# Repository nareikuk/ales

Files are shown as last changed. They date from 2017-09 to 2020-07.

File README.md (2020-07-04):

# ales
Altitude Limiting Electronic Switch for model electric glider competitions

This is still under early development even though it has been under construction since 2016. The aim is to produce a cheap,
easy to construct and simple to use altitude limiting switch for electric motor launched model gliders for competition use.
The schematics, PCB and firmware are all provided. I may be able to supply blank PCBs or even fully populated PCBs in the future,
once the bugs have been ironed out and I'm happy that the project has reached a production quality level.

Note that currently the firmware is working but some improvements required around startup reliability.

The current features of the ALES v2 include:
1) Pre-set altitude cut-off of 100m, 150m or 200m which are the three standards used in competition.
2) Motor run time limited to 30 seconds if pre-set altitude has not been reached before then
3) Auto-calibrates to receiver pulse timing at start up
4) Auto-calibrates altitude of launch field
5) After cut-off, if throttle stick is retuned to idle, the ALES will re-enable motor power after three seconds for those landing emergencies
6) Altitude sampling at 1kHz with better than 0.2m resolution
7) Very small and light hardware profile
8) Works with HV or standard servos and is powered from the receiver, drawing around 2mA
9) 32-bit STM32F0 microcontroller and BMP280 pressure sensor provide the core functionality
10) Single-sided load for all surface mount components

Future features once v2 has reached production quality will include anti-zoom control and field based configuration.

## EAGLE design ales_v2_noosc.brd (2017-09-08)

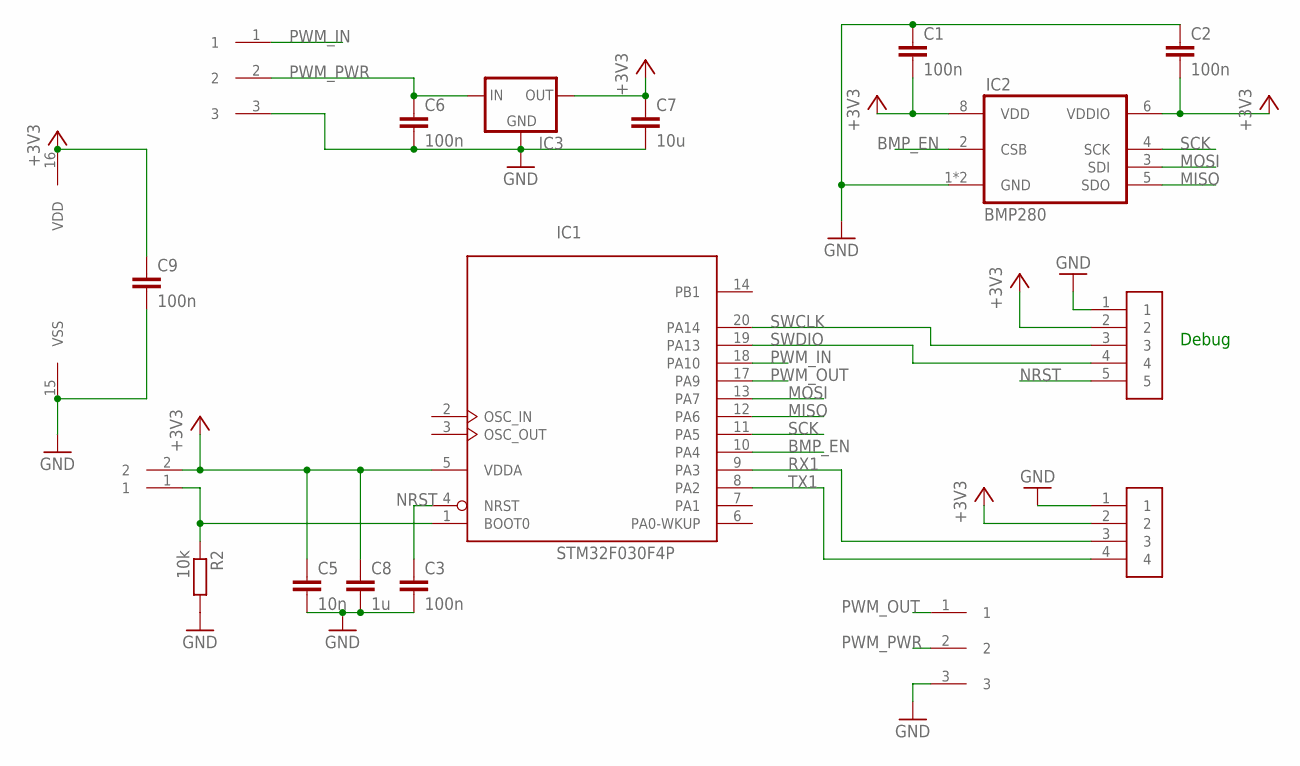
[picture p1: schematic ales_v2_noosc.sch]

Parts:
BOOT: SMD_CONN1X2; CONN_SMD1X2
C1, C2, C3, C6, C9: 100n; C0603K
C5: 10n; C0603K
C7: 10u; C0603K
C8: 1u; C0603K
IC1: STM32F030F4P; TSSOP20-I
IC2: BMP280
IC3: XC63FPM; SOT23
R2: 10k; R0603
U$2, U$3: CONN1X3
U$4: CONN1X4
U$6: CONN1X5

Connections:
+3V3: BOOT.2, C1.2, C2.2, C5.1, C7.1, C8.1, C9.1, IC1.5 (VDDA), IC1.16 (VDD), IC2.6 (VDDIO), IC2.8 (VDD), IC3.1 (OUT), U$4.2, U$6.2
BMP_EN: IC1.10 (PA4), IC2.2 (CSB)
BOOT0: BOOT.1, IC1.1 (BOOT0), R2.1
GND: C1.1, C2.1, C3.2, C5.2, C6.2, C7.2, C8.2, C9.2, IC1.15 (VSS), IC2.1 (GND), IC2.7 (GND), IC3.3 (GND), R2.2, U$2.3, U$3.3, U$4.1, U$6.1
MISO: IC1.12 (PA6), IC2.5 (SDO)
MOSI: IC1.13 (PA7), IC2.3 (SDI)
NRST: C3.1, IC1.4 (NRST), U$6.5
PWM_IN: IC1.18 (PA10), U$3.1
PWM_OUT: IC1.17 (PA9), U$2.1
PWM_PWR: C6.1, IC3.2 (IN), U$2.2, U$3.2
RX1: IC1.9 (PA3), U$4.3
SCK: IC1.11 (PA5), IC2.4 (SCK)
SWCLK: IC1.20 (PA14), U$6.3
SWDIO: IC1.19 (PA13), U$6.4
TX1: IC1.8 (PA2), U$4.4

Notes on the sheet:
Debug

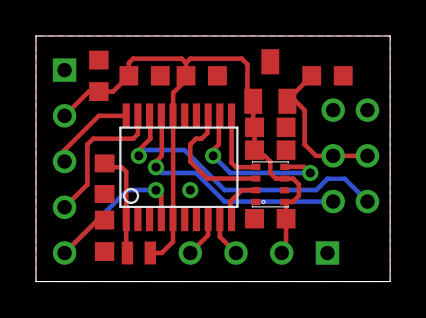
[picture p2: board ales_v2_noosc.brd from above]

Board: 2 copper layers, 19.7 x 13.6 mm, 17 parts (0 on the bottom side), 15 nets.

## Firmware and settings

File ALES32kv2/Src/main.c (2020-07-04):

/**
 ******************************************************************************
 * File Name          : main.c
 * Description        : Main program body
 ******************************************************************************
 *
 * COPYRIGHT(c) 2016 STMicroelectronics
 *
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
 ******************************************************************************
 */
/* Includes ------------------------------------------------------------------*/
#include "stm32f0xx_hal.h"

/* USER CODE BEGIN Includes */
#include "string.h"
/* USER CODE END Includes */

SPI_HandleTypeDef hspi1;

TIM_HandleTypeDef htim1;

UART_HandleTypeDef huart1;

/* USER CODE BEGIN PV */
//SPI_HandleTypeDef SpiHandle;
typedef struct _bmp280calibration {
    uint16_t dig_t1;
    int16_t dig_t2;
    int16_t dig_t3;
    uint16_t dig_p1;
    int16_t dig_p2;
    int16_t dig_p3;
    int16_t dig_p4;
    int16_t dig_p5;
    int16_t dig_p6;
    int16_t dig_p7;
    int16_t dig_p8;
    int16_t dig_p9;
} Bmp280Calibration;

Bmp280Calibration bmpCalibration;

//#define BUFFERSIZE 64

// Pressure differences * 25600 between start alt and height above start alt
#define ALT_100M -1196     // -305995.1386
#define ALT_150M -1789     // -457892.7898
#define ALT_200M -2380     // -609060.7514

#define ALT_CUTOFF ALT_150M    // Change this to set the altimeter cutoff height
#define VERSION "1.4f"

#define RCSAMPLES 8

//#define VERBOSE 1

enum {
    BMP280_REGISTER_DIG_T1 = 0x88,
    BMP280_REGISTER_DIG_T2 = 0x8A,
    BMP280_REGISTER_DIG_T3 = 0x8C,

    BMP280_REGISTER_DIG_P1 = 0x8E,
    BMP280_REGISTER_DIG_P2 = 0x90,
    BMP280_REGISTER_DIG_P3 = 0x92,
    BMP280_REGISTER_DIG_P4 = 0x94,
    BMP280_REGISTER_DIG_P5 = 0x96,
    BMP280_REGISTER_DIG_P6 = 0x98,
    BMP280_REGISTER_DIG_P7 = 0x9A,
    BMP280_REGISTER_DIG_P8 = 0x9C,
    BMP280_REGISTER_DIG_P9 = 0x9E,

    BMP280_REGISTER_CHIPID = 0xD0,
    BMP280_REGISTER_VERSION = 0xD1,
    BMP280_REGISTER_SOFTRESET = 0xE0,

    BMP280_REGISTER_CAL26 = 0xE1,  // R calibration stored in 0xE1-0xF0

    BMP280_REGISTER_CONTROL = 0xF4,
    BMP280_REGISTER_CONFIG = 0xF5,
    BMP280_REGISTER_PRESSUREDATA = 0xF7,
    BMP280_REGISTER_TEMPDATA = 0xFA,
};

typedef int32_t BMP280_S32_t;
typedef uint32_t BMP280_U32_t;
typedef int64_t BMP280_S64_t;

BMP280_S32_t t_fine;
volatile int rxPwm = 0;
int lastCounter = 0;
int counter = 0;

uint8_t throttleActive = 0; // The throttle is allowed to be moved from idle if throttleActive is 1
#ifdef VERBOSE
char strbuf[100];
#endif
/* USER CODE END PV */

void SystemClock_Config(void);
void errorHandler(void);
static void MX_GPIO_Init(void);
static void MX_SPI1_Init(void);
static void MX_TIM1_Init(void);
static void MX_USART1_UART_Init(void);

void HAL_TIM_MspPostInit(TIM_HandleTypeDef *htim);

/* USER CODE BEGIN PFP */
uint8_t bmp280GetChipId(void);
uint8_t bmp280GetCalibration(void);
int32_t spiGetInt20(uint8_t address);
void bmp280Init(void);
BMP280_S32_t bmp280CompensateTemperature(BMP280_S32_t adcTemp);
BMP280_S64_t bmp280PressureDiff(BMP280_S32_t adcPres, BMP280_S64_t startPa);
void timeoutErrorHandler(void);
void itoa(int n, char s[]);

/* USER CODE END PFP */

/* USER CODE BEGIN 0 */
int tFilter[RCSAMPLES] = { 0 };
uint8_t filterCount = 0;

void HAL_TIM_IC_CaptureCallback(TIM_HandleTypeDef *htim) {
    int diff = 0;

    if (htim->Instance == TIM1) {
        // Ideally we'd like to know if the interrupt was due to the rising or falling edge
        // so we can capture the pulse time on the falling edge and start the counter on
        // the rising edge. Until that is figured out, go for a simpler version where we capture
        // two edges and see if the time is short enough to have been a pulse rather than the
        // gap between pulses. A pulse will be shorter than 2500uS (probably only around 2100uS
        // at most). The gap between pulses will be at least 17500uS.
        counter = HAL_TIM_ReadCapturedValue(htim, TIM_CHANNEL_3);
        if (lastCounter > counter) {
            diff = 20000 - lastCounter + counter;
        } else {
            diff = counter - lastCounter;
        }
        lastCounter = counter;

        if (diff < 2500 && diff > 900) { // We must have the pulse time rather than the gap between pulses
            tFilter[filterCount++] = diff;
            filterCount %= RCSAMPLES;

            int avg = 0;
            for (int i = 0; i < RCSAMPLES; i++) {
                avg += tFilter[i];
            }

            rxPwm = avg / RCSAMPLES;
        }

        // TODO: if no pulses received for some time, then set rxPwm to 0 rather than leaving
        //       it stuck at last measured value
    }
}

int waitForIdleThrottle() {
    // Capture idle throttle. Must be below 1200uS and above 900uS for 2 seconds
    uint8_t idleCaptured = 0;
    int idleThrottlePeriod;

    while (!idleCaptured) {
        int throttle = rxPwm;
        while (throttle > 1200 || throttle < 900) {
            HAL_Delay(100);
            throttle = rxPwm;
#ifdef VERBOSE
            strcpy(strbuf, "Waiting for thr1:");
            itoa(throttle, &strbuf[strlen(strbuf)]);
            strcat(strbuf, "\n");
            HAL_UART_Transmit(&huart1, (uint8_t*) strbuf, strlen(strbuf), 5000);
#endif
        }
        int throttlePeriod = throttle;
        uint8_t captureTime = 0;
        while ((throttle >= throttlePeriod && (throttle - throttlePeriod) < 25)
                || (throttle < throttlePeriod
                        && (throttlePeriod - throttle) < 25)) {
            captureTime++;
            if (captureTime > 20) {
                // Wait 2 seconds for stable throttle position
                idleCaptured = 1;
                idleThrottlePeriod = throttle;
                break;
            }
#ifdef VERBOSE
            strcpy(strbuf, "Waiting for thr2:");
            itoa(throttle, &strbuf[strlen(strbuf)]);
            strcat(strbuf, "\n");
            HAL_UART_Transmit(&huart1, (uint8_t*) strbuf, strlen(strbuf), 5000);
#endif
            HAL_Delay(100);
            throttle = rxPwm;
        }
    }

    return idleThrottlePeriod;
}

/* USER CODE END 0 */

int main(void) {

    /* USER CODE BEGIN 1 */
    int32_t temperature;
    int idleThrottlePeriod = 1000;
    /* USER CODE END 1 */

    /* MCU Configuration----------------------------------------------------------*/

    /* Reset of all peripherals, Initializes the Flash interface and the Systick. */
    HAL_Init();

    /* Configure the system clock */
    SystemClock_Config();

    HAL_Delay(2000);

    /* Initialize all configured peripherals */
    MX_GPIO_Init();
    MX_SPI1_Init();
    MX_TIM1_Init();
    MX_USART1_UART_Init();

    /* USER CODE BEGIN 2 */
    // Start PWM_IN capture
    HAL_TIM_IC_Start_IT(&htim1, TIM_CHANNEL_3);

    // Capture idle throttle. Must be below 1200uS and above 900uS for 2 seconds
    idleThrottlePeriod = waitForIdleThrottle();

    // Start PWM_OUT timer: TIM1, Ch2
    HAL_TIM_PWM_Start(&htim1, TIM_CHANNEL_2);
    __HAL_TIM_SET_COMPARE(&htim1, TIM_CHANNEL_2, idleThrottlePeriod); // Set throttle to idle
    throttleActive = 1;

    bmp280GetCalibration();
    bmp280Init();

    BMP280_S64_t startPressure = 0;
    int pressureCaptureCount = 0;
    int throttleIdleCount = 0;
    int throttleOnTime = 0;
    int loopCount = 0;
    /* USER CODE END 2 */

    /* Infinite loop */
    /* USER CODE BEGIN WHILE */
    while (1) {
        /* USER CODE END WHILE */

        /* USER CODE BEGIN 3 */

        HAL_GPIO_TogglePin(LOOP_TICK_GPIO_Port, LOOP_TICK_Pin);

        // Record loop time and make sure it runs at 1mS per loop
        uint32_t tickstart = HAL_GetTick();
        int throttle = rxPwm;

        if (loopCount % 100 == 0) {
            int32_t rawTemperature = spiGetInt20(BMP280_REGISTER_TEMPDATA);
            int32_t rawPressure = spiGetInt20(BMP280_REGISTER_PRESSUREDATA);

            temperature = bmp280CompensateTemperature(rawTemperature);
            BMP280_S64_t pressureDiff = bmp280PressureDiff(rawPressure,
                    startPressure);

            if (startPressure == 0 && pressureDiff > 0) {
                pressureCaptureCount++;
                if (pressureCaptureCount > 10) {
                    pressureCaptureCount = 10;
                    startPressure = pressureDiff; // TODO: Check if pressure has been stable for 1 second
#ifdef VERBOSE
                    strcpy(strbuf, "Start press:");
                    itoa(startPressure, &strbuf[strlen(strbuf)]);
                    strcat(strbuf, "\n");
                    HAL_UART_Transmit(&huart1, (uint8_t *) strbuf,
                            strlen(strbuf), 5000);
#endif
                }
            }

            // Check pressureDiff to see if the max altitude has been reached.
            // PressureDiff is lower (more negative) with increasing altitude
            // TODO: Verify altitude is stable or increasing rather than a 'glitch'
            if ((pressureDiff <= ALT_CUTOFF) && throttleActive) {
                throttleActive = 0;    // Force ESC to idle
                throttleOnTime = 0;    // Reset on time
#ifdef VERBOSE
                strcpy(strbuf, "Max alt reached\n");
                HAL_UART_Transmit(&huart1, (uint8_t *) strbuf, strlen(strbuf),
                        5000);
#endif
            }

#ifdef VERBOSE
            int32_t temp1 = temperature / 100;
            int32_t temp2 = temperature - temp1 * 100;

            strcpy(strbuf, VERSION);
            strcat(strbuf, ",T:");
            itoa(temp1, &strbuf[strlen(strbuf)]);
            strcat(strbuf, ".");
            itoa(temp2, &strbuf[strlen(strbuf)]);
            strcat(strbuf, "C,P:");
            itoa(pressureDiff, &strbuf[strlen(strbuf)]);
            strcat(strbuf, ",PWMIn:");
            itoa(throttle, &strbuf[strlen(strbuf)]);
            strcat(strbuf, ",OnTime:");
            itoa(throttleOnTime, &strbuf[strlen(strbuf)]);
            strcat(strbuf, ",Active:");
            itoa(throttleActive, &strbuf[strlen(strbuf)]);
            strcat(strbuf, ",IdleCount:");
            itoa(throttleIdleCount, &strbuf[strlen(strbuf)]);
            strcat(strbuf, ",IdlePeriod:");
            itoa(idleThrottlePeriod, &strbuf[strlen(strbuf)]);
            strcat(strbuf, "\n");

            HAL_UART_Transmit(&huart1, (uint8_t *) strbuf, strlen(strbuf),
                    5000);
#endif
        }

        // Check if throttle is above idle
        if (throttleActive && throttle >= idleThrottlePeriod + 40) {
            //startTime = getCurrentTime();
            throttleIdleCount = 0;
            throttleOnTime++;
            if (throttleOnTime >= 30000) {
                throttleActive = 0; // Force throttle to idle if it's been on for more than 30 seconds
#ifdef VERBOSE
                strcpy(strbuf, "Max time reached\n");
                HAL_UART_Transmit(&huart1, (uint8_t *) strbuf, strlen(strbuf),
                        5000);
#endif
            }
        }

        // Check for throttle going to idle during active time
        if (throttleActive && throttle <= idleThrottlePeriod + 25) {
            throttleActive = 0;    // Force throttle to idle
            throttleOnTime = 0;    // Reset throttle on time
#ifdef VERBOSE
            if (loopCount % 500 == 0) {
                strcpy(strbuf, "Thr idle\n");
                HAL_UART_Transmit(&huart1, (uint8_t *) strbuf, strlen(strbuf),
                        5000);
            }
#endif
        }

        // Check if throttle has been disarmed and has been set to idle for more than 3 seconds
        if (throttleActive == 0 && throttle <= idleThrottlePeriod + 25) {
            throttleIdleCount++;
            if (throttleIdleCount > 3000) {
                throttleIdleCount = 3000;
                throttleActive = 1; // Throttle is re-armed if it's been idle for more than 3 seconds
#ifdef VERBOSE
                if (loopCount % 500 == 0) {
                    strcpy(strbuf, "Thr re-armed\n");
                    HAL_UART_Transmit(&huart1, (uint8_t *) strbuf,
                            strlen(strbuf), 5000);
                }
#endif
            }
        }

        // Pass throttle to ESC if it is armed, otherwise force ESC to idle
        if (throttleActive) {
            __HAL_TIM_SET_COMPARE(&htim1, TIM_CHANNEL_2, throttle);
        } else {
            __HAL_TIM_SET_COMPARE(&htim1, TIM_CHANNEL_2, idleThrottlePeriod);
        }

        loopCount++;
        loopCount %= 1000;

        while ((HAL_GetTick() - tickstart) < 1) // 1mS delay for entire loop - ensure rest of loop takes less than 1mS though!
        {
        }

    }
    /* USER CODE END 3 */

}

/** System Clock Configuration
 */
void SystemClock_Config(void) {

    RCC_OscInitTypeDef RCC_OscInitStruct;
    RCC_ClkInitTypeDef RCC_ClkInitStruct;
    RCC_PeriphCLKInitTypeDef PeriphClkInit;

    RCC_OscInitStruct.OscillatorType = RCC_OSCILLATORTYPE_HSI;
    RCC_OscInitStruct.HSIState = RCC_HSI_ON;
    RCC_OscInitStruct.HSICalibrationValue = 16;
    RCC_OscInitStruct.PLL.PLLState = RCC_PLL_ON;
    RCC_OscInitStruct.PLL.PLLSource = RCC_PLLSOURCE_HSI;
    RCC_OscInitStruct.PLL.PLLMUL = RCC_PLL_MUL12;
    RCC_OscInitStruct.PLL.PREDIV = RCC_PREDIV_DIV1;
    if (HAL_RCC_OscConfig(&RCC_OscInitStruct) != HAL_OK) {
        errorHandler();
    }

    RCC_ClkInitStruct.ClockType = RCC_CLOCKTYPE_HCLK | RCC_CLOCKTYPE_SYSCLK
            | RCC_CLOCKTYPE_PCLK1;
    RCC_ClkInitStruct.SYSCLKSource = RCC_SYSCLKSOURCE_PLLCLK;
    RCC_ClkInitStruct.AHBCLKDivider = RCC_SYSCLK_DIV1;
    RCC_ClkInitStruct.APB1CLKDivider = RCC_HCLK_DIV1;
    if (HAL_RCC_ClockConfig(&RCC_ClkInitStruct, FLASH_LATENCY_1) != HAL_OK) {
        errorHandler();
    }

    PeriphClkInit.PeriphClockSelection = RCC_PERIPHCLK_USART1;
    PeriphClkInit.Usart1ClockSelection = RCC_USART1CLKSOURCE_PCLK1;
    if (HAL_RCCEx_PeriphCLKConfig(&PeriphClkInit) != HAL_OK) {
        errorHandler();
    }

    HAL_SYSTICK_Config(HAL_RCC_GetHCLKFreq() / 1000);

    HAL_SYSTICK_CLKSourceConfig (SYSTICK_CLKSOURCE_HCLK);

    /* SysTick_IRQn interrupt configuration */
    HAL_NVIC_SetPriority(SysTick_IRQn, 0, 0);
}

/* SPI1 init function */
static void MX_SPI1_Init(void) {

    hspi1.Instance = SPI1;
    hspi1.Init.Mode = SPI_MODE_MASTER;
    hspi1.Init.Direction = SPI_DIRECTION_2LINES;
    hspi1.Init.DataSize = SPI_DATASIZE_8BIT;
    hspi1.Init.CLKPolarity = SPI_POLARITY_HIGH;
    hspi1.Init.CLKPhase = SPI_PHASE_2EDGE;
    hspi1.Init.NSS = SPI_NSS_SOFT;
    hspi1.Init.BaudRatePrescaler = SPI_BAUDRATEPRESCALER_4;
    hspi1.Init.FirstBit = SPI_FIRSTBIT_MSB;
    hspi1.Init.TIMode = SPI_TIMODE_DISABLE;
    hspi1.Init.CRCCalculation = SPI_CRCCALCULATION_DISABLE;
    hspi1.Init.CRCPolynomial = 7;
    hspi1.Init.CRCLength = SPI_CRC_LENGTH_DATASIZE;
    hspi1.Init.NSSPMode = SPI_NSS_PULSE_DISABLE;
    if (HAL_SPI_Init(&hspi1) != HAL_OK) {
        errorHandler();
    }

}

/* TIM1 init function */
static void MX_TIM1_Init(void) {

    TIM_MasterConfigTypeDef sMasterConfig;
    TIM_OC_InitTypeDef sConfigOC;
    TIM_IC_InitTypeDef sConfigIC;
    TIM_BreakDeadTimeConfigTypeDef sBreakDeadTimeConfig;

    htim1.Instance = TIM1;
    htim1.Init.Prescaler = 47;
    htim1.Init.CounterMode = TIM_COUNTERMODE_UP;
    htim1.Init.Period = 19999;
    htim1.Init.ClockDivision = TIM_CLOCKDIVISION_DIV1;
    htim1.Init.RepetitionCounter = 0;
    if (HAL_TIM_PWM_Init(&htim1) != HAL_OK) {
        errorHandler();
    }

    if (HAL_TIM_IC_Init(&htim1) != HAL_OK) {
        errorHandler();
    }

    sMasterConfig.MasterOutputTrigger = TIM_TRGO_RESET;
    sMasterConfig.MasterSlaveMode = TIM_MASTERSLAVEMODE_DISABLE;
    if (HAL_TIMEx_MasterConfigSynchronization(&htim1, &sMasterConfig)
            != HAL_OK) {
        errorHandler();
    }

    sConfigOC.OCMode = TIM_OCMODE_PWM1;
    sConfigOC.Pulse = 0;
    sConfigOC.OCPolarity = TIM_OCPOLARITY_HIGH;
    sConfigOC.OCNPolarity = TIM_OCNPOLARITY_HIGH;
    sConfigOC.OCFastMode = TIM_OCFAST_DISABLE;
    sConfigOC.OCIdleState = TIM_OCIDLESTATE_RESET;
    sConfigOC.OCNIdleState = TIM_OCNIDLESTATE_RESET;
    if (HAL_TIM_PWM_ConfigChannel(&htim1, &sConfigOC, TIM_CHANNEL_2)
            != HAL_OK) {
        errorHandler();
    }

    sConfigIC.ICPolarity = TIM_INPUTCHANNELPOLARITY_BOTHEDGE;
    sConfigIC.ICSelection = TIM_ICSELECTION_DIRECTTI;
    sConfigIC.ICPrescaler = TIM_ICPSC_DIV1;
    sConfigIC.ICFilter = 0;
    if (HAL_TIM_IC_ConfigChannel(&htim1, &sConfigIC, TIM_CHANNEL_3) != HAL_OK) {
        errorHandler();
    }

    sBreakDeadTimeConfig.OffStateRunMode = TIM_OSSR_DISABLE;
    sBreakDeadTimeConfig.OffStateIDLEMode = TIM_OSSI_DISABLE;
    sBreakDeadTimeConfig.LockLevel = TIM_LOCKLEVEL_OFF;
    sBreakDeadTimeConfig.DeadTime = 0;
    sBreakDeadTimeConfig.BreakState = TIM_BREAK_DISABLE;
    sBreakDeadTimeConfig.BreakPolarity = TIM_BREAKPOLARITY_HIGH;
    sBreakDeadTimeConfig.AutomaticOutput = TIM_AUTOMATICOUTPUT_DISABLE;
    if (HAL_TIMEx_ConfigBreakDeadTime(&htim1, &sBreakDeadTimeConfig)
            != HAL_OK) {
        errorHandler();
    }

    HAL_TIM_MspPostInit(&htim1);

}

/* USART1 init function */
static void MX_USART1_UART_Init(void) {

    huart1.Instance = USART1;
    huart1.Init.BaudRate = 38400;
    huart1.Init.WordLength = UART_WORDLENGTH_8B;
    huart1.Init.StopBits = UART_STOPBITS_1;
    huart1.Init.Parity = UART_PARITY_NONE;
    huart1.Init.Mode = UART_MODE_TX_RX;
    huart1.Init.HwFlowCtl = UART_HWCONTROL_NONE;
    huart1.Init.OverSampling = UART_OVERSAMPLING_16;
    huart1.Init.OneBitSampling = UART_ONE_BIT_SAMPLE_DISABLE;
    huart1.AdvancedInit.AdvFeatureInit = UART_ADVFEATURE_NO_INIT;
    if (HAL_UART_Init(&huart1) != HAL_OK) {
        errorHandler();
    }

}

/** Configure pins as 
 * Analog 
 * Input 
 * Output
 * EVENT_OUT
 * EXTI
 */
static void MX_GPIO_Init(void) {

    GPIO_InitTypeDef GPIO_InitStruct;

    /* GPIO Ports Clock Enable */
    __HAL_RCC_GPIOA_CLK_ENABLE();
    __HAL_RCC_GPIOB_CLK_ENABLE();

    /*Configure GPIO pin Output Level */
    HAL_GPIO_WritePin(SPI_EN_GPIO_Port, SPI_EN_Pin, GPIO_PIN_RESET);

    /*Configure GPIO pin Output Level */
    HAL_GPIO_WritePin(LOOP_TICK_GPIO_Port, LOOP_TICK_Pin, GPIO_PIN_RESET);

    /*Configure GPIO pin : SPI_EN_Pin */
    GPIO_InitStruct.Pin = SPI_EN_Pin;
    GPIO_InitStruct.Mode = GPIO_MODE_OUTPUT_PP;
    GPIO_InitStruct.Pull = GPIO_NOPULL;
    GPIO_InitStruct.Speed = GPIO_SPEED_FREQ_HIGH;
    HAL_GPIO_Init(SPI_EN_GPIO_Port, &GPIO_InitStruct);

    /*Configure GPIO pin : LOOP_TICK_Pin */
    GPIO_InitStruct.Pin = LOOP_TICK_Pin;
    GPIO_InitStruct.Mode = GPIO_MODE_OUTPUT_PP;
    GPIO_InitStruct.Pull = GPIO_NOPULL;
    GPIO_InitStruct.Speed = GPIO_SPEED_FREQ_LOW;
    HAL_GPIO_Init(LOOP_TICK_GPIO_Port, &GPIO_InitStruct);

}

/* USER CODE BEGIN 4 */
/* reverse:  reverse string s in place */
void reverse(char s[]) {
    int c, i, j;

    for (i = 0, j = strlen(s) - 1; i < j; i++, j--) {
        c = s[i];
        s[i] = s[j];
        s[j] = c;
    }
}

/* itoa:  convert n to characters in s */
void itoa(int n, char s[]) {
    int i;
    uint8_t negative = 0;

    if (n < 0) { /* record sign */
        n = -n; /* make n positive */
        negative = 1;
    }

    i = 0;
    do { /* generate digits in reverse order */
        s[i++] = n % 10 + '0'; /* get next digit */
    } while ((n /= 10) > 0); /* delete it */

    if (negative) {
        s[i++] = '-';
    }

    s[i] = '\0';

    reverse(s);
}

uint8_t bmp280GetChipId(void) {
    uint8_t txbuf[2];
    uint8_t rxbuf[2];
    HAL_SPI_StateTypeDef status;

    txbuf[0] = 0x80 | BMP280_REGISTER_CHIPID;
    txbuf[1] = 0xFF;

    rxbuf[0] = 0x00;
    rxbuf[1] = 0x00;

    HAL_GPIO_WritePin(SPI_EN_GPIO_Port, SPI_EN_Pin, GPIO_PIN_RESET);

    status = HAL_SPI_TransmitReceive(&hspi1, txbuf, rxbuf, 2, 5000);
    if (status == HAL_SPI_STATE_ERROR) {
        errorHandler();
    }

    HAL_GPIO_WritePin(SPI_EN_GPIO_Port, SPI_EN_Pin, GPIO_PIN_SET);

    return rxbuf[1];
}

int32_t spiGetInt20(uint8_t address) {
    uint8_t txbuf[4];
    uint8_t rxbuf[4];
    HAL_SPI_StateTypeDef status;

    txbuf[0] = 0x80 | address;
    txbuf[1] = 0xFF;
    txbuf[2] = 0xFF;
    txbuf[3] = 0xFF;

    rxbuf[0] = 0x00;
    rxbuf[1] = 0x00;
    rxbuf[2] = 0x00;
    rxbuf[3] = 0x00;

    HAL_GPIO_WritePin(SPI_EN_GPIO_Port, SPI_EN_Pin, GPIO_PIN_RESET);

    status = HAL_SPI_TransmitReceive(&hspi1, txbuf, rxbuf, 4, 5000);
    if (status == HAL_SPI_STATE_ERROR) {
        errorHandler();
    }

    HAL_GPIO_WritePin(SPI_EN_GPIO_Port, SPI_EN_Pin, GPIO_PIN_SET);

    int32_t val = rxbuf[1] << 16 | rxbuf[2] << 8 | (rxbuf[3] & 0xF0);
    return val >> 4;
}

uint8_t bmp280GetCalibration(void) {
    uint8_t txbuf[25];
    uint8_t rxbuf[25];
    HAL_SPI_StateTypeDef status;

    txbuf[0] = 0x80 | BMP280_REGISTER_DIG_T1;
    for (int i = 1; i < 25; i++) {
        txbuf[i] = 0xFF;
    }

    for (int i = 0; i < 25; i++) {
        rxbuf[i] = 0x00;
    }

    HAL_GPIO_WritePin(SPI_EN_GPIO_Port, SPI_EN_Pin, GPIO_PIN_RESET);

    status = HAL_SPI_TransmitReceive(&hspi1, txbuf, rxbuf, 25, 5000);
    if (status == HAL_SPI_STATE_ERROR) {
        errorHandler();
    }

    HAL_GPIO_WritePin(SPI_EN_GPIO_Port, SPI_EN_Pin, GPIO_PIN_SET);

    bmpCalibration.dig_t1 = rxbuf[2] << 8 | rxbuf[1];
    bmpCalibration.dig_t2 = rxbuf[4] << 8 | rxbuf[3];
    bmpCalibration.dig_t3 = rxbuf[6] << 8 | rxbuf[5];
    bmpCalibration.dig_p1 = rxbuf[8] << 8 | rxbuf[7];
    bmpCalibration.dig_p2 = rxbuf[10] << 8 | rxbuf[9];
    bmpCalibration.dig_p3 = rxbuf[12] << 8 | rxbuf[11];
    bmpCalibration.dig_p4 = rxbuf[14] << 8 | rxbuf[13];
    bmpCalibration.dig_p5 = rxbuf[16] << 8 | rxbuf[15];
    bmpCalibration.dig_p6 = rxbuf[18] << 8 | rxbuf[17];
    bmpCalibration.dig_p7 = rxbuf[20] << 8 | rxbuf[19];
    bmpCalibration.dig_p8 = rxbuf[22] << 8 | rxbuf[21];
    bmpCalibration.dig_p9 = rxbuf[24] << 8 | rxbuf[23];

    return 0;
}
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

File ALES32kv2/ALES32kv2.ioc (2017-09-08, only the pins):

Mcu.UserName=STM32F031F6Px
PA10.GPIO_Label=PWM_IN
PA10.Signal=S_TIM1_CH3
PA13.Signal=SYS_SWDIO
PA14.Signal=SYS_SWCLK
PA2.Signal=USART1_TX
PA3.Signal=USART1_RX
PA4.GPIO_Label=SPI_EN
PA4.Signal=GPIO_Output
PA5.Signal=SPI1_SCK
PA6.Signal=SPI1_MISO
PA7.Signal=SPI1_MOSI
PA9.GPIO_Label=PWM_OUT
PA9.Signal=S_TIM1_CH2
PB1.GPIO_Label=LOOP_TICK
PB1.Signal=GPIO_Output

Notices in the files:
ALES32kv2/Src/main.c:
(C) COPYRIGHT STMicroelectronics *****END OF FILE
